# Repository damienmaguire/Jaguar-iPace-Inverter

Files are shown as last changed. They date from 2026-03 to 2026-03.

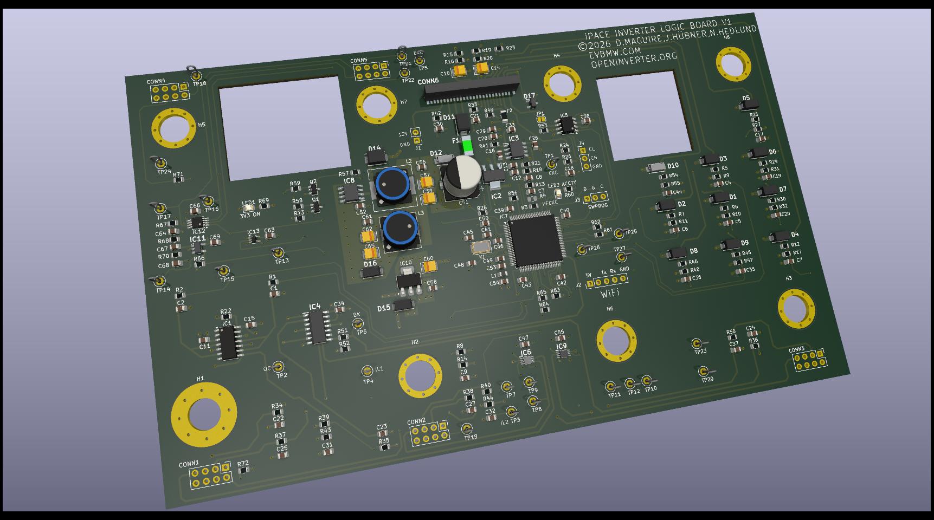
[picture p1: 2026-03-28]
Front/FDU_V1/FDU_V1_3D.jpg

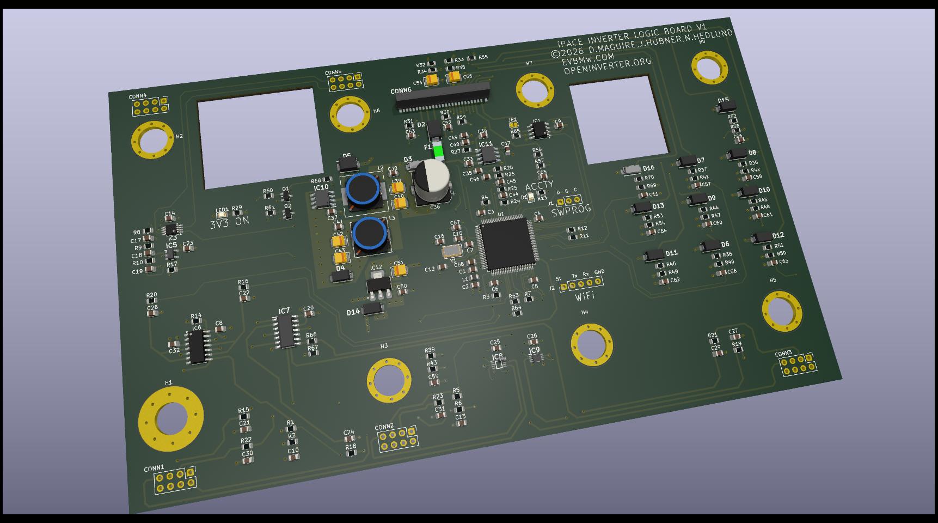
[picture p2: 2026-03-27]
Front/FDU_V1/FDU_V1_Tracked.jpg

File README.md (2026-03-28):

# Jaguar-iPace-Inverter
Design of Opensource Logic boards to run the Jaguar iPace Inverter and Motors.

PCB Designs in Kicad 9 format.

Front inverter used in the iPace is acuallly a Vitesco EPF2.8+ :
https://vitesco-technologies.com/en/Home/Solutions/Products/High-Voltage-Inverter-(EPF2-8-)-en

Reverse engineering thread on the openinverter forum :
https://openinverter.org/forum/viewtopic.php?f=23&t=1210

Videos :
https://youtu.be/Kg5qWuOF9P8

10/10/25 : Add prelim front drive unit V1 board design (work in progress).

25/03/26 : PCB Layout in progress.

FDU_V1

28/03/26 : Layout done. First prototypes ordered from JLCPCB.

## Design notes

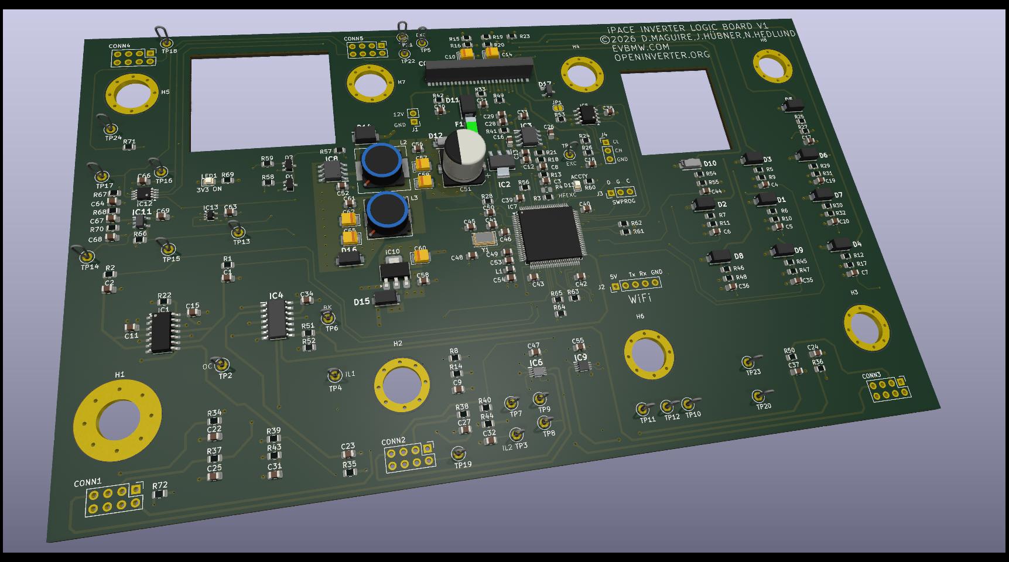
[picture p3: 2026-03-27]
Front/FDU_V1/FDU_V1_Final.jpg

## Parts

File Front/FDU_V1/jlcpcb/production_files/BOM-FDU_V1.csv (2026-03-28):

Comment | Designator | Footprint | LCSC | Quantity
0.1uF | C11,C34,C38,C39,C40,C42,C43,C46,C47,C48,C49,C50,C53,C55,C63,C66,C69 | C_0805_2012Metric | C126469 | 17
0R | R49 | R_0805_2012Metric | C17477 | 1
100R | R71,R72 | R_0805_2012Metric | C17408 | 2
100uF 6.3V | C10,C14,C57,C59,C60,C62,C65 | CP_EIA-3528-15_AVX-H | C7195 | 7
10K | R1,R17,R2,R21,R27,R33,R42,R56,R63,R66,R73 | R_0805_2012Metric | C17414 | 10
10R | R41 | R_0805_2012Metric | C17415 | 1
10nF | C15,C22,C23,C24,C25,C27,C37 | C_0805_2012Metric | C1710 | 7
10uF | C16,C33,C58 | C_0805_2012Metric | C15850 | 3
10uH 0805 | L1 | L_0805_2012Metric | C88172 | 1
1206L050/24WR | F2 | Fuse_1206_3216Metric | C2154056 | 1
120R | R53 | R_0805_2012Metric | C17437 | 1
150pF | C68 | C_0805_2012Metric | C107111 | 1
1K | R58,R59 | R_0805_2012Metric | C149504 | 2
1K | R28,R45,R46,R47,R48,R51,R61,R62,R67 | R_0805_2012Metric | C17513 | 8
1K2 | R12,R23,R24,R25,R8 | R_0805_2012Metric | C114526 | 5
1K5 | R10,R11,R31,R32,R55,R9 | R_0805_2012Metric | C114555 | 6
1K8 | R13,R18 | R_0805_2012Metric | C114222 | 2
1N5 | C64 | C_0805_2012Metric | C1717 | 1
1nF | C21,C30,C31,C32,C61 | C_0805_2012Metric | C94121 | 5
1uF | C1,C17,C18,C19,C2,C20,C26,C35,C36,C4,C5,C52,C54,C56,C6,C7,C9 | C_0805_2012Metric | C215803 | 17
1uF 25V | C44 | C_0805_2012Metric | C116352 | 1
220R | R15,R16,R19,R20 | R_0805_2012Metric | C17557 | 4
22nF | C12,C13,C28,C29,C3,C8 | C_0805_2012Metric | C1729 | 6
27K | R57 | R_0805_2012Metric | C17593 | 1
27pF | C41,C45 | C_0805_2012Metric | C1808 | 2
2K | R52 | R_0805_2012Metric | C17604 | 1
2K2 | R14,R22,R26 | R_0805_2012Metric | C114561 | 3
2K6 | R43,R44 | R_0805_2012Metric | C144568 | 2
330Pf | C67 | C_0805_2012Metric | C107116 | 1
3K9 | R3,R64 | R_0805_2012Metric | C114221 | 2
LEDS | LED1,LED2 | LED_0805_2012Metric | C84256 | 2
3uH | L3 | L_10.4x10.4_H4.8 | C31964 | 1
470uF 25V | C51 | CP_Elec_10x10 | C46550466 | 1
47K | R65 | R_0805_2012Metric | C17713 | 1
4K7 | R29,R30,R5,R54,R6,R7 | R_0805_2012Metric | C60816 | 6
560R | R34,R35,R36,R37,R38,R50 | R_0805_2012Metric | C28636 | 6
5K1 | R70 | R_0805_2012Metric | C84375 | 1
680R | R60,R69 | R_0805_2012Metric | C17798 | 2
68uH | L2 | L_12x12mm_H8mm | C9907 | 1
6K2 | R39,R40 | R_0805_2012Metric | C114535 | 2
6K8 | R68 | R_0805_2012Metric | C137409 | 1
8MHz | Y1 | Crystal_SMD_5032-2Pin_5.0x3.2mm | C115962 | 1
AMS1117-3.3 | IC10 | SOT-223-3_TabPin2 | C6186 | 1
CD74HC30M96 | IC4 | SOIC127P600X175-14N | C6540 | 1
ESDCAN01-2BLY | D17 | SOT95P255X150-3N | C53340814 | 1
FH12-50S-0.5SVA_54_ | CONN6 | FH1250S05SVA54 | C597991 | 1
JFC2410-0500TS | F1 | FUSC6126X280N | C136377 | 1
LM2901 | IC1 | SOIC-14_3.9x8.7mm_P1.27mm | C7932 | 1
MCP6291T-E_OT | IC11 | SOT95P280X145-5N | C145575 | 1
MMBT3904 | Q1,Q2 | SOT-23 | C20526 | 2
NCV8452STT3G | IC2 | SOT230P700X180-4N | C477982 | 1
SMAJ18CA | D10,D12 | DIONM5127X229N | C10768 | 2
SMAJ5.0A | D1,D15,D2,D3,D4,D5,D6,D7,D8,D9 | DIOM5127X229N | C83329 | 10
SMAJ7.0A | D16 | DIOM5026X229N | C138782 | 1
SN65HVD230 | IC5 | SOIC-8_3.9x4.9mm_P1.27mm | C12084 | 1
SN74LVC1G125DCK | IC13 | Texas_R-PDSO-G5_DCK-5 | C7833 | 1
SN74LVC3G04DCUR | IC9 | SOP50P310X90-8N | C153799 | 1
SN74LVC3G17DCTR | IC12,IC6 | MSOP-8_3x3mm_P0.65mm | C18213 | 2
SS54B | D11,D14 | DIOM5336X244N | C32513 | 2
STM32F103VCTx | IC7 | LQFP-100_14x14mm_P0.5mm | C53327627 | 1
TDA2822D | IC3 | SOIC127P600X175-8N | C668663 | 1
XL1509-5.0E1 | IC8 | SOIC127P600X175-8N | C61063 | 1

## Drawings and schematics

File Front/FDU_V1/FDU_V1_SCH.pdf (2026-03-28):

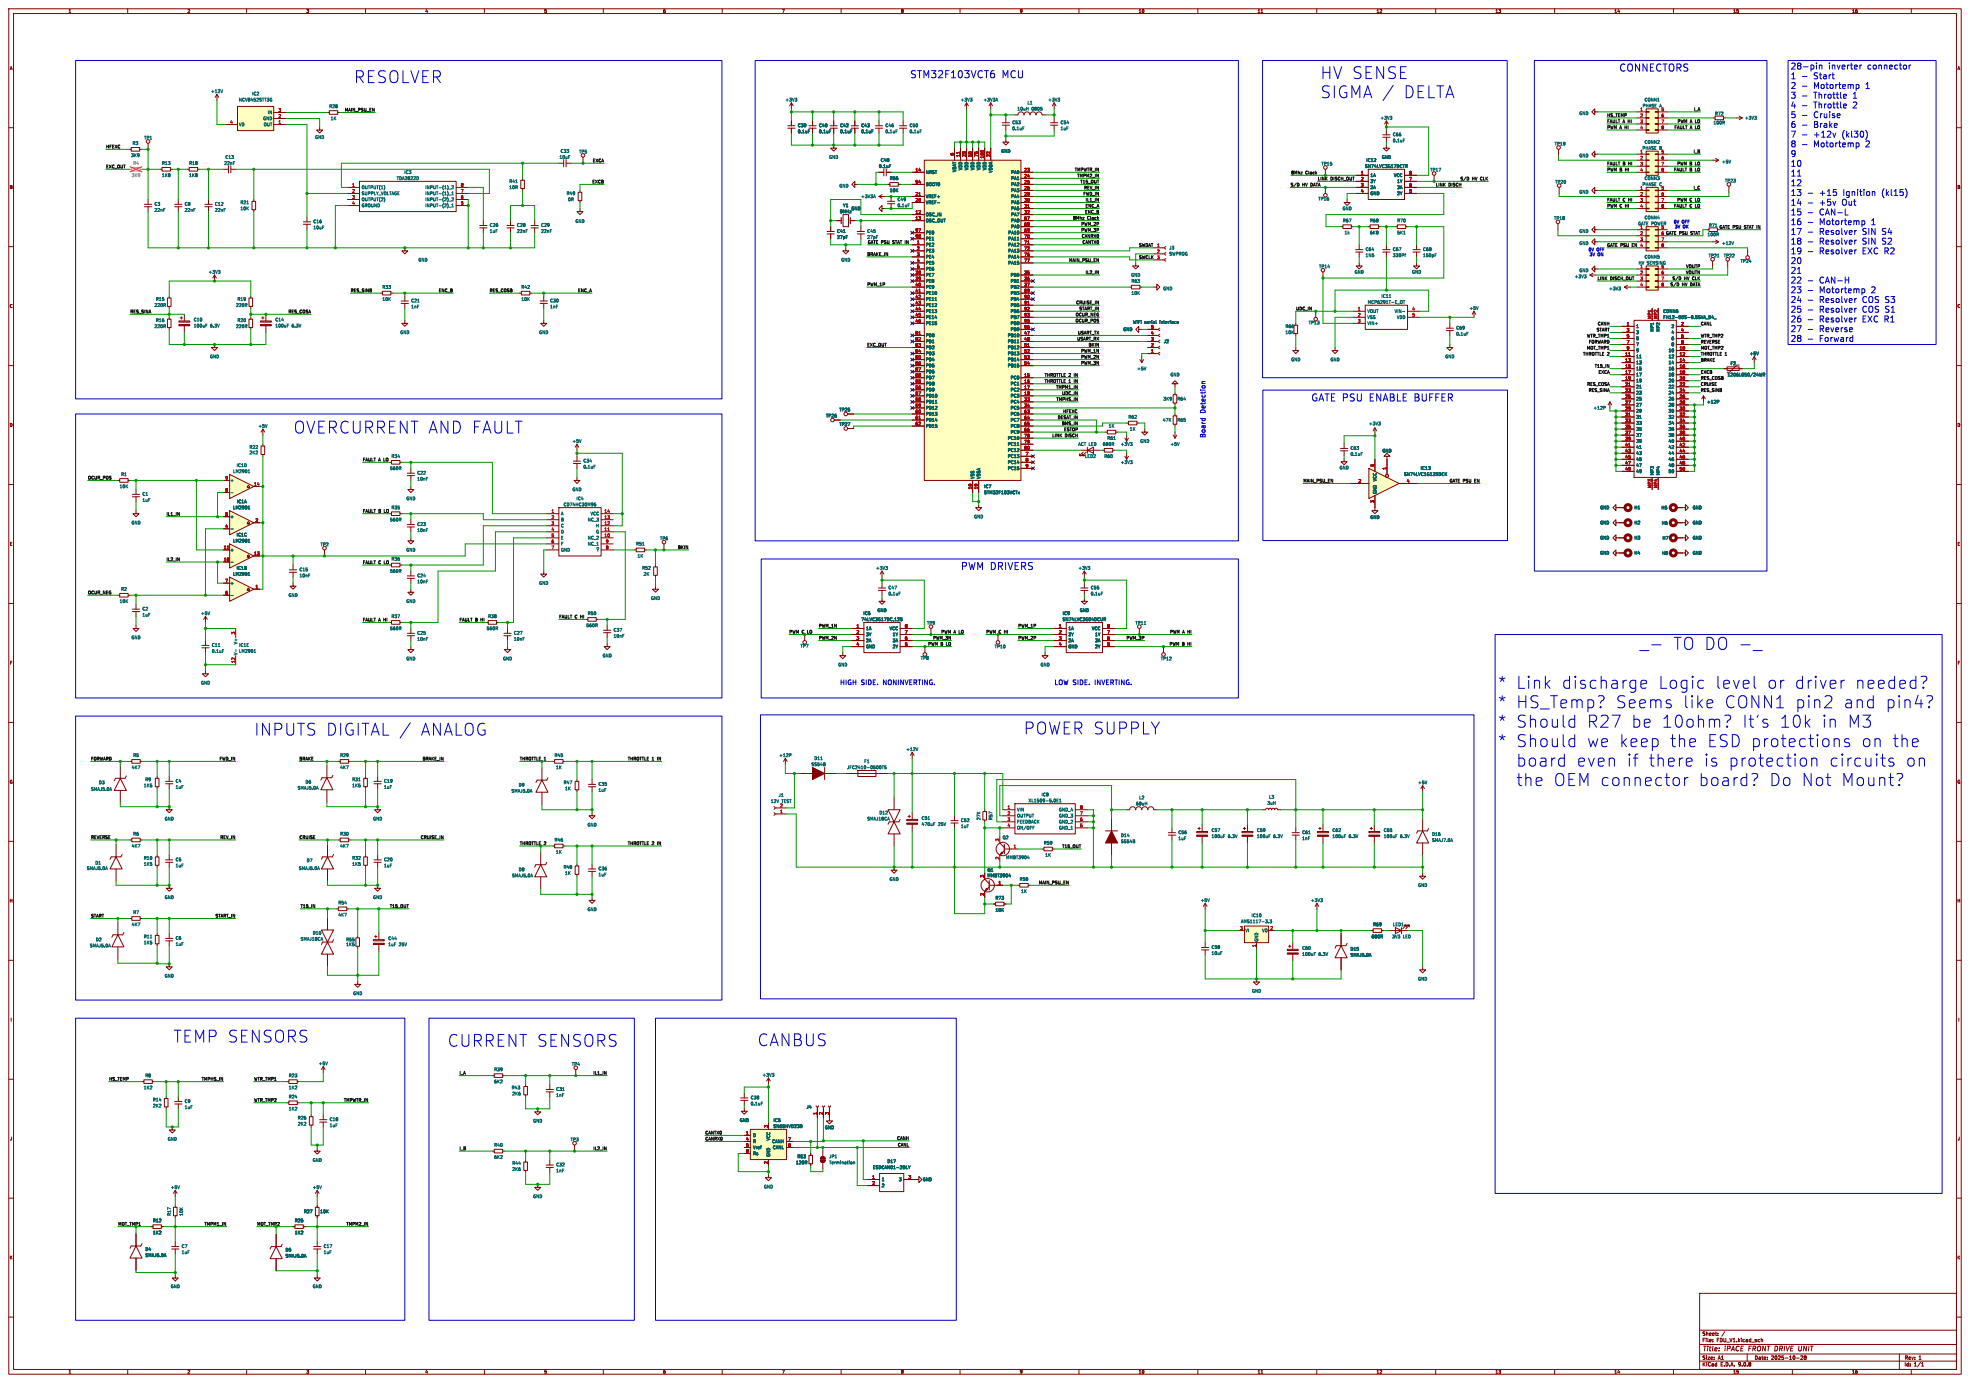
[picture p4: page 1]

6 VDD 11 VDD 28 VDD 50 VSS 10 VDD 75 VSSA 19 VDD 100 VDDA 22 PA0

FAULT B HI FAULT C HI

PWM B HI MOT_TMP1 PWM C LO

GATE PSU ENABLE BUFFER

PWM A HI FAULT A LO

* Link discharge Logic level or driver needed?
* HS_Temp? Seems like CONN1 pin2 and pin4?
* Should R27 be 10ohm? It's 10k in M3
the OEM connector board? Do Not Mount?

File: FDU_V1.kicad_sch Sheet: /
Id: 1/1 Title: iPACE FRONT DRIVE UNIT

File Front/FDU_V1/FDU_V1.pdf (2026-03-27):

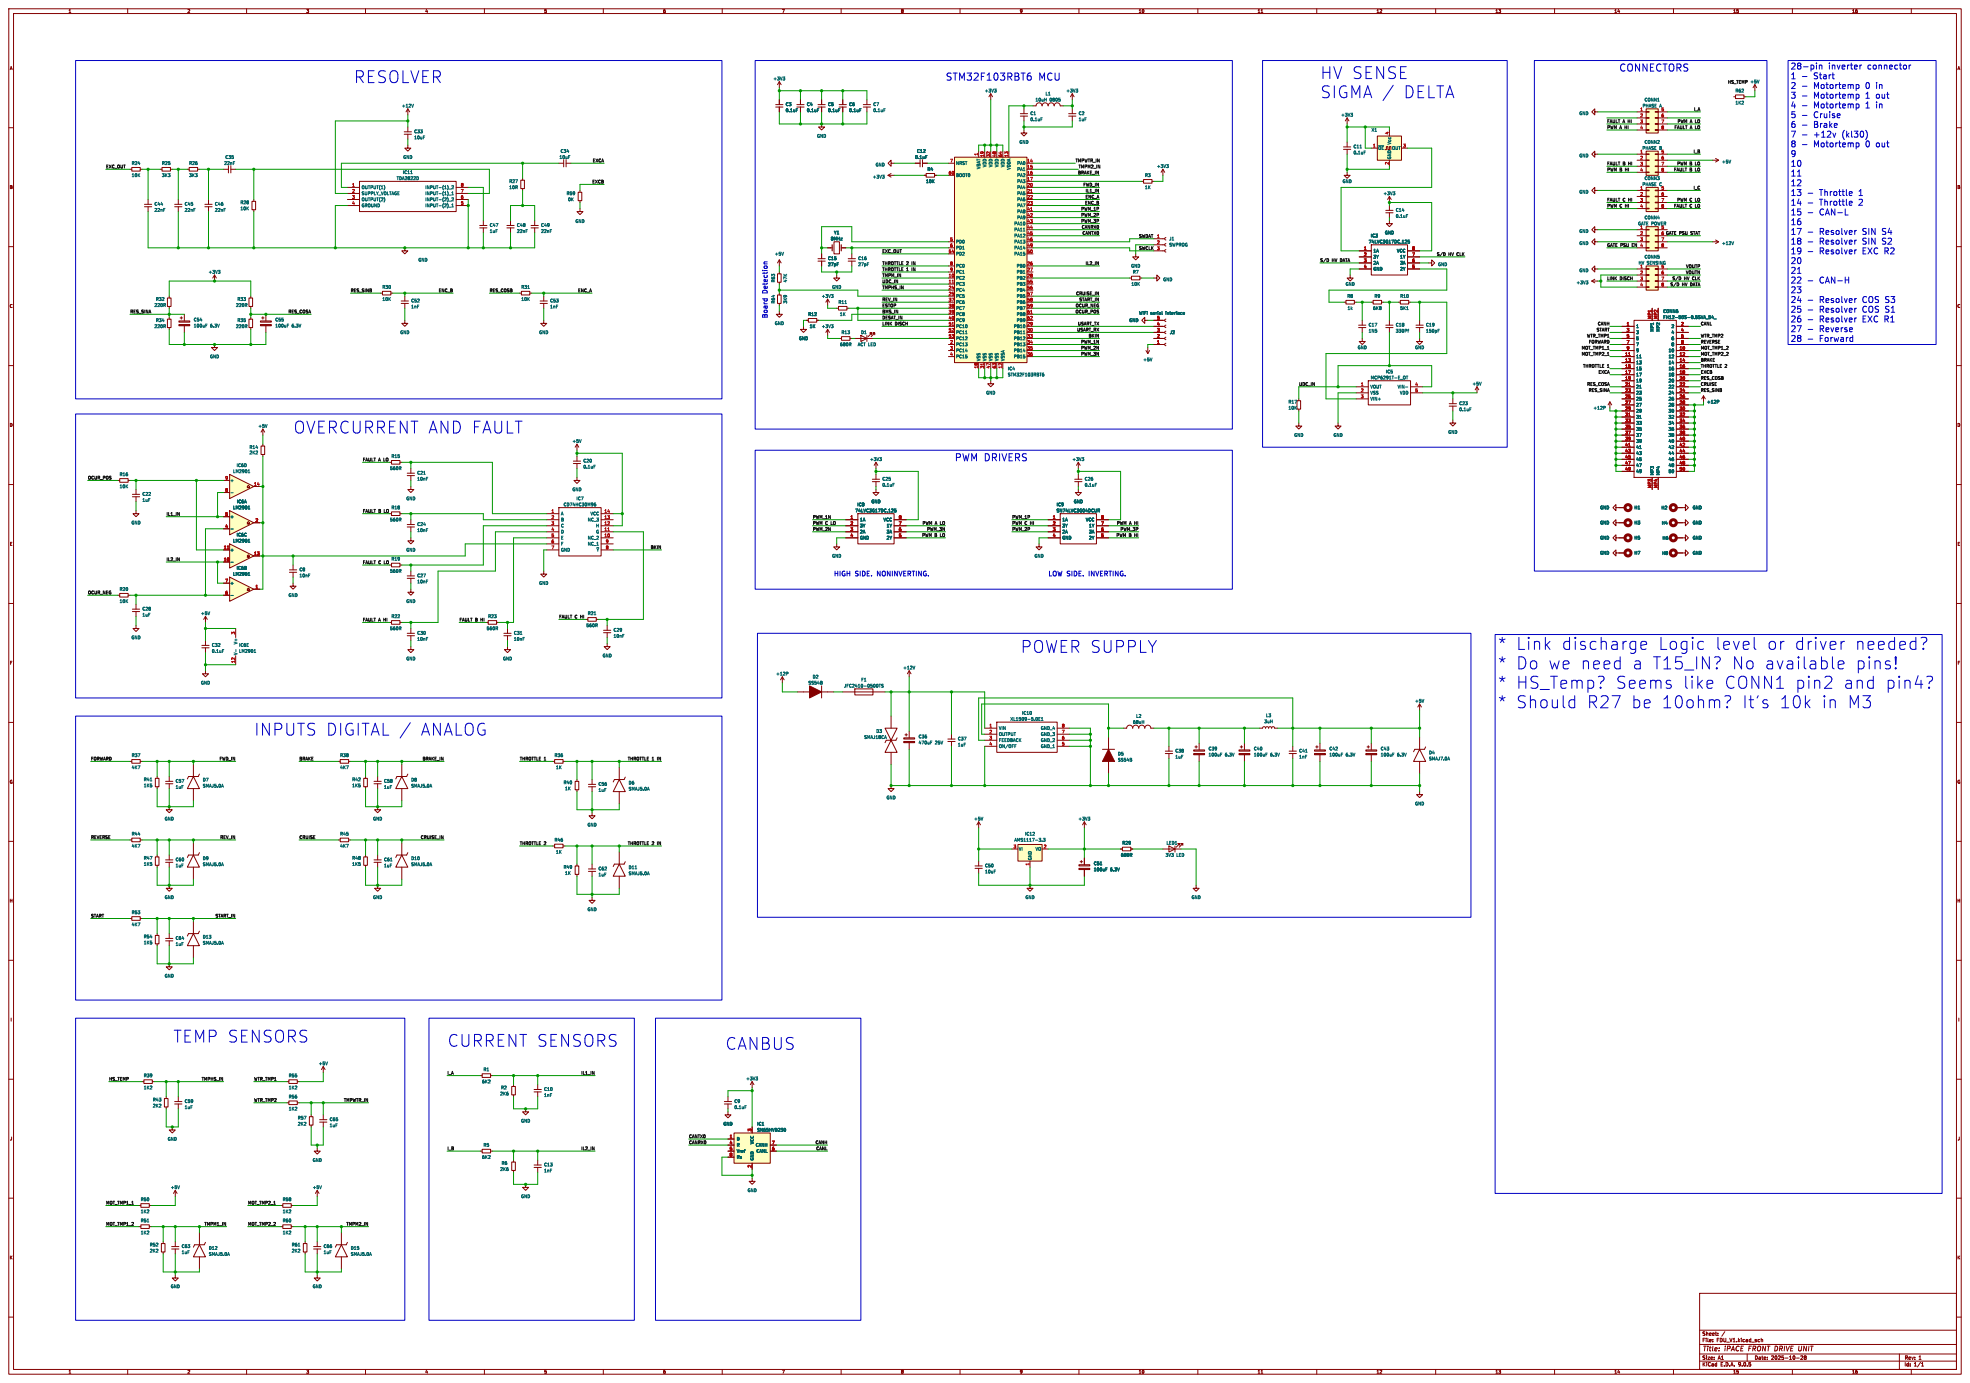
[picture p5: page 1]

HS_TEMP * Link discharge Logic level or driver needed?

1 VSS 18 VDD 19 VSS 31 VDD 32 VSS 47 VDD 48 VSS 63 VDD 64 VSSA 12 VDDA 13 PA0

FAULT C HI PWM C HI GATE PSU EN

* Do we need a T15_IN? No available pins!
* HS_Temp? Seems like CONN1 pin2 and pin4?
* Should R27 be 10ohm? It's 10k in M3

File: FDU_V1.kicad_sch Sheet: /
Id: 1/1 Title: iPACE FRONT DRIVE UNIT

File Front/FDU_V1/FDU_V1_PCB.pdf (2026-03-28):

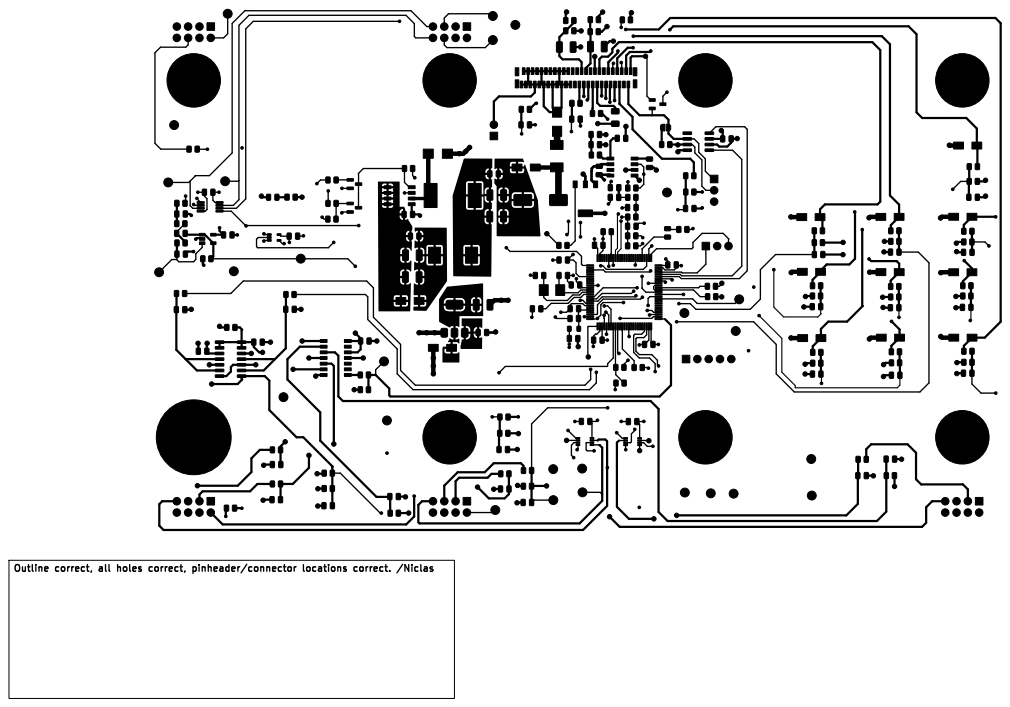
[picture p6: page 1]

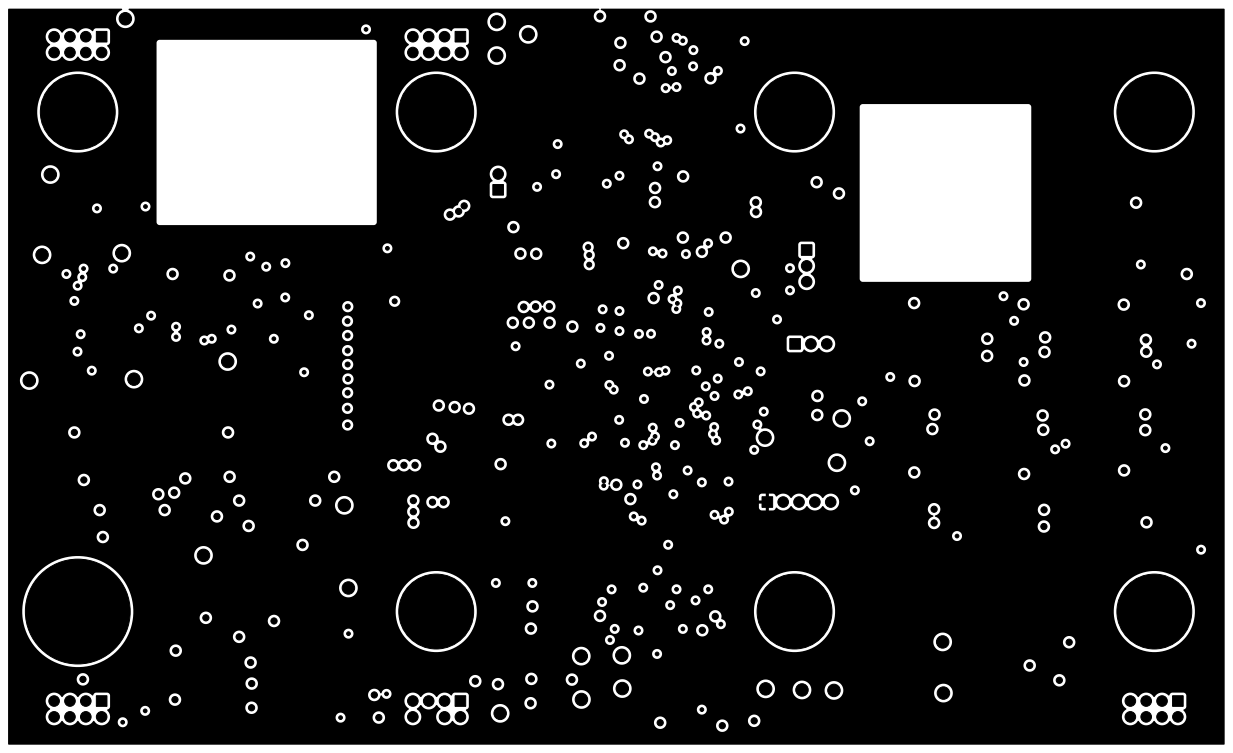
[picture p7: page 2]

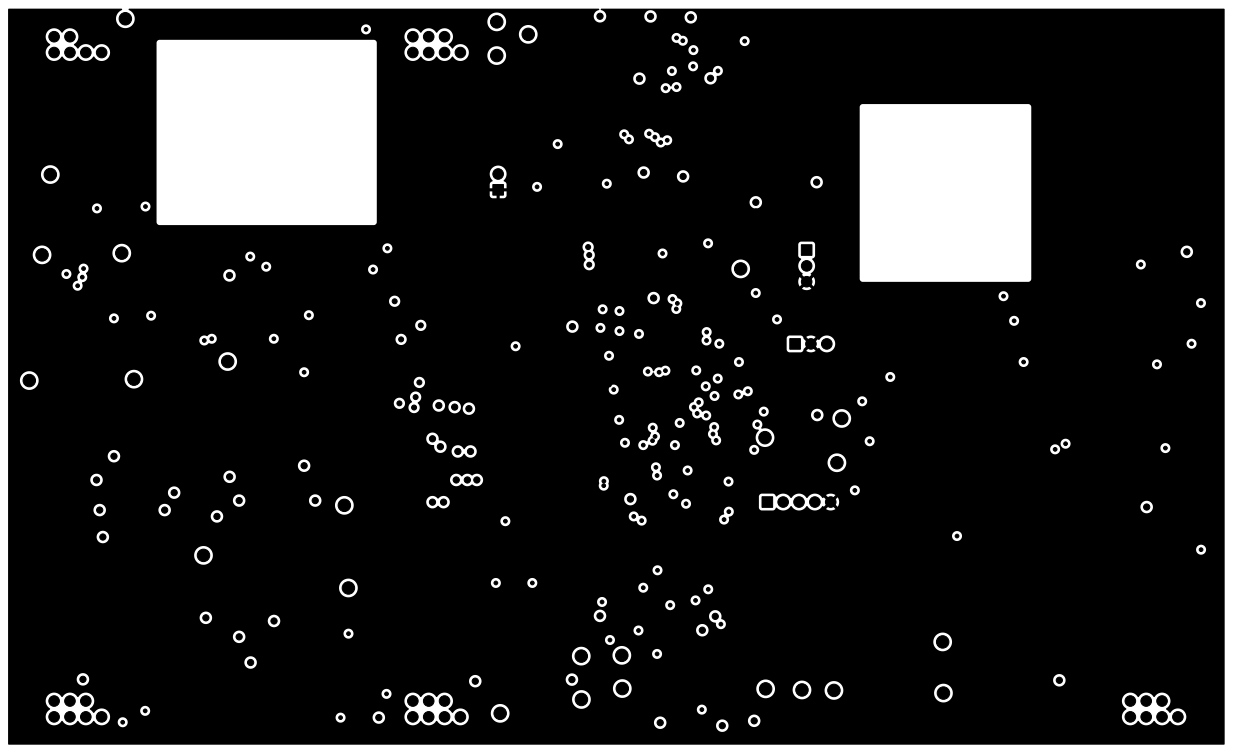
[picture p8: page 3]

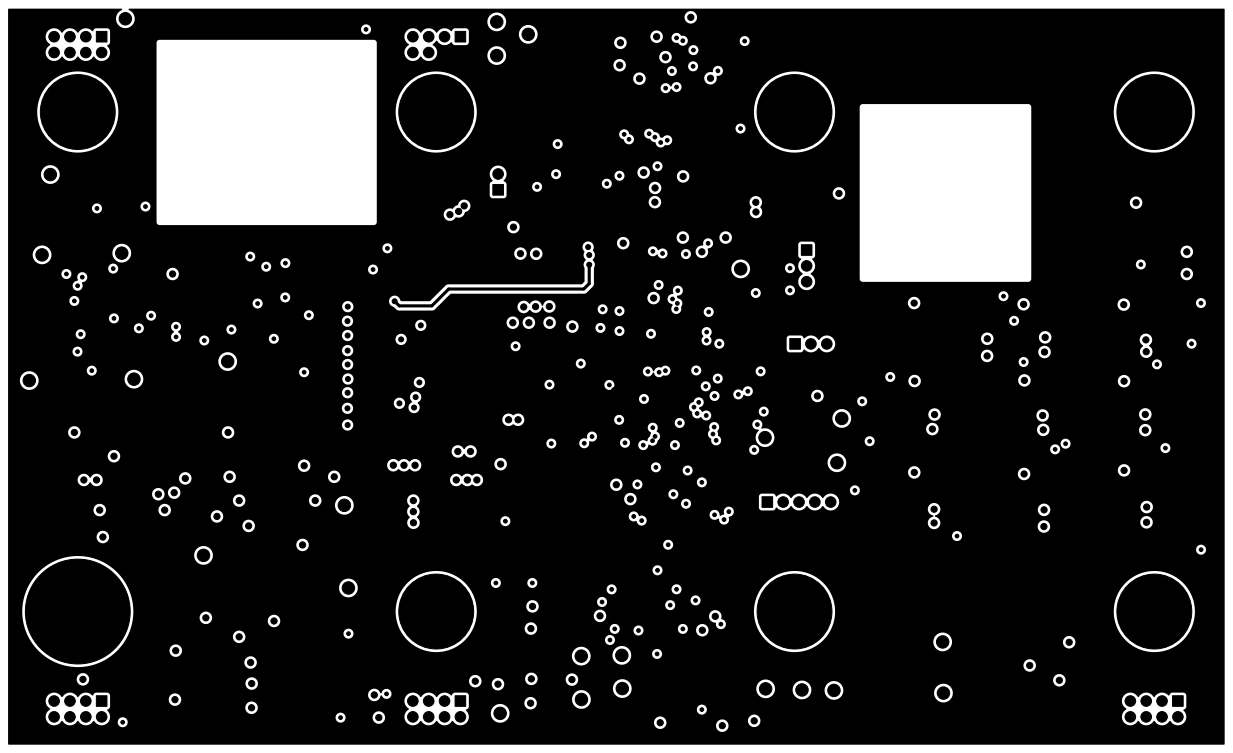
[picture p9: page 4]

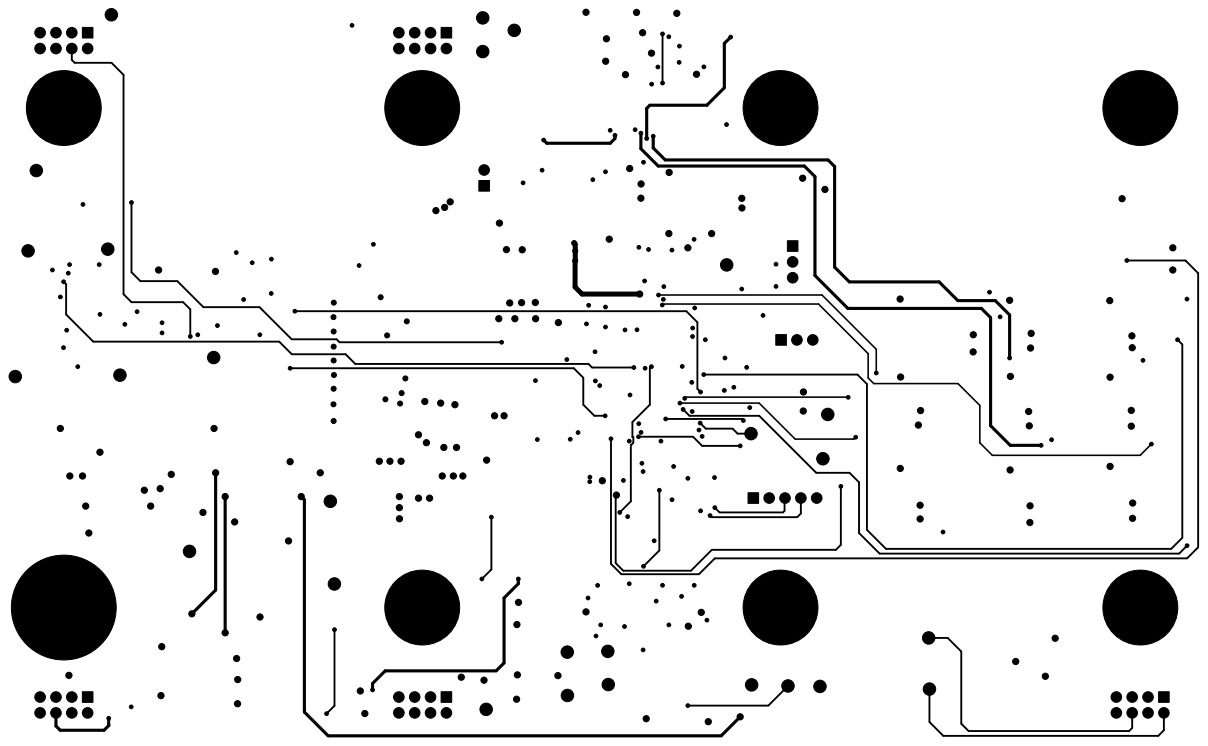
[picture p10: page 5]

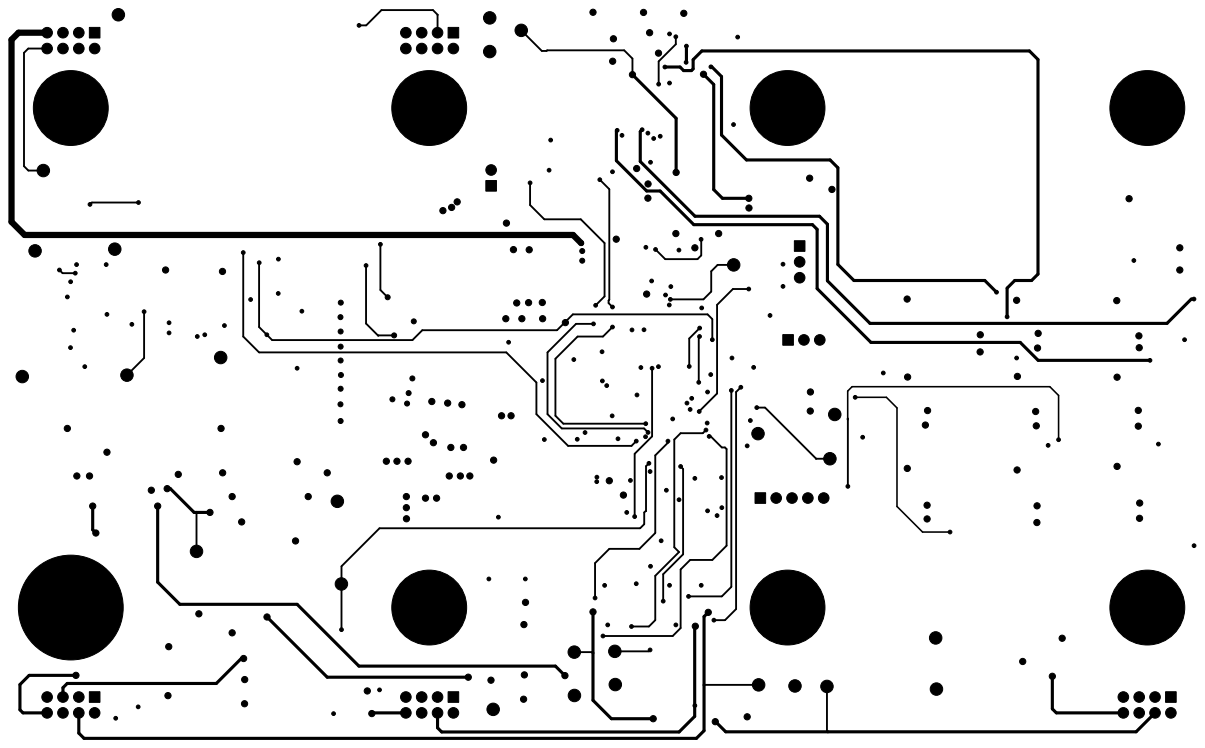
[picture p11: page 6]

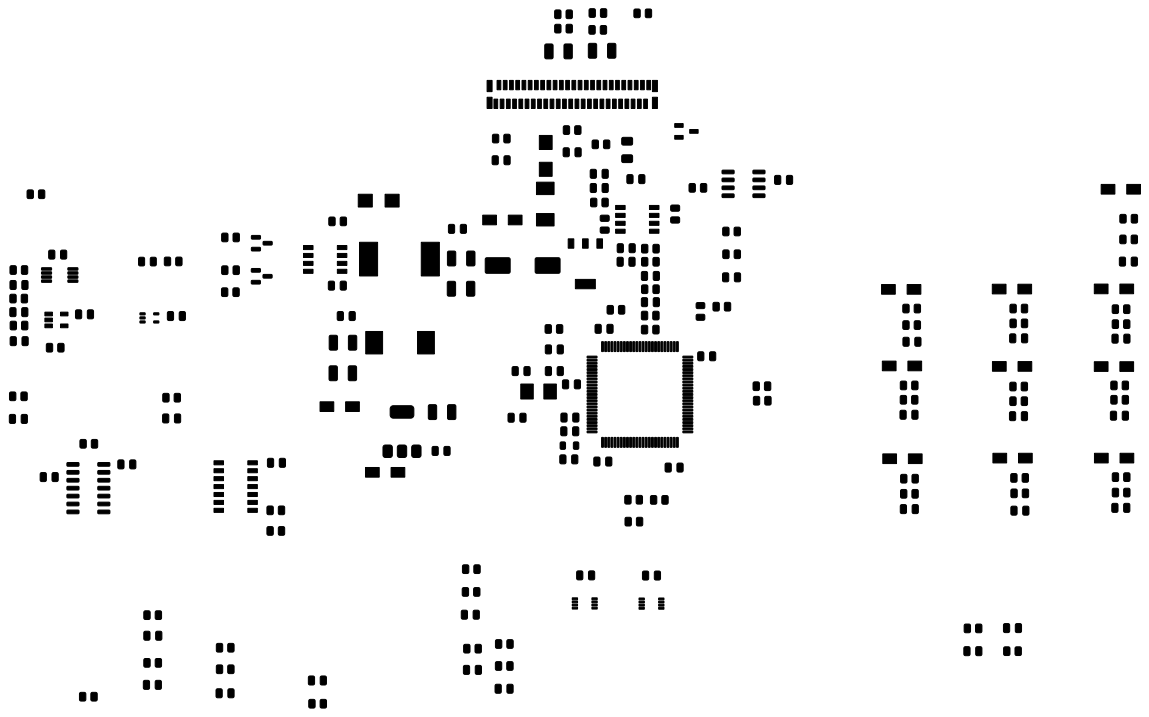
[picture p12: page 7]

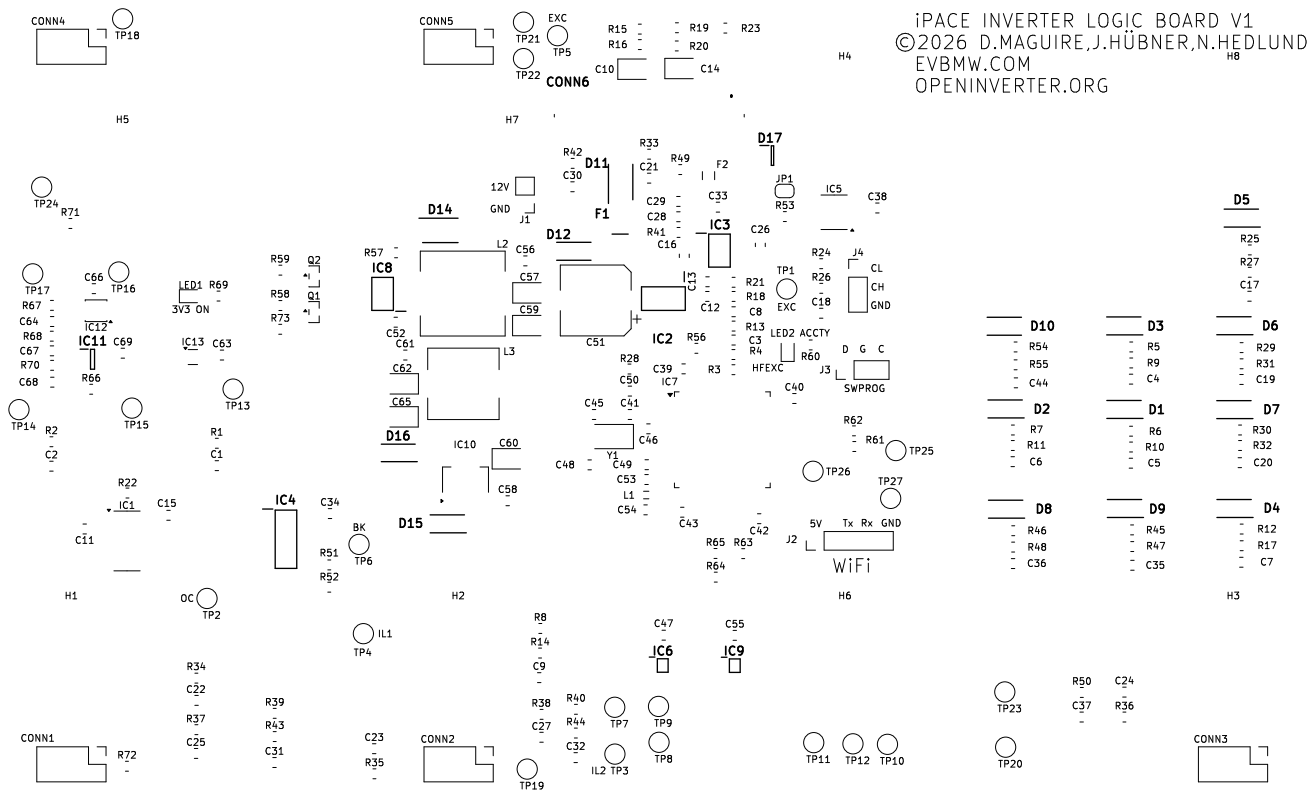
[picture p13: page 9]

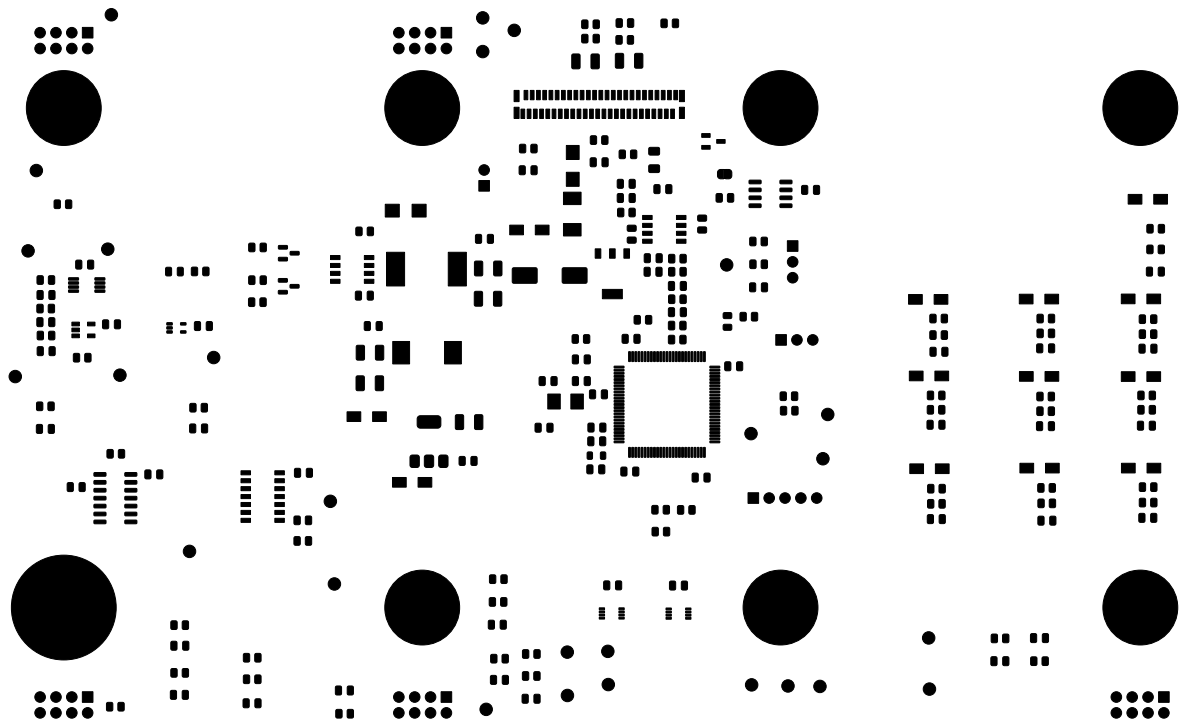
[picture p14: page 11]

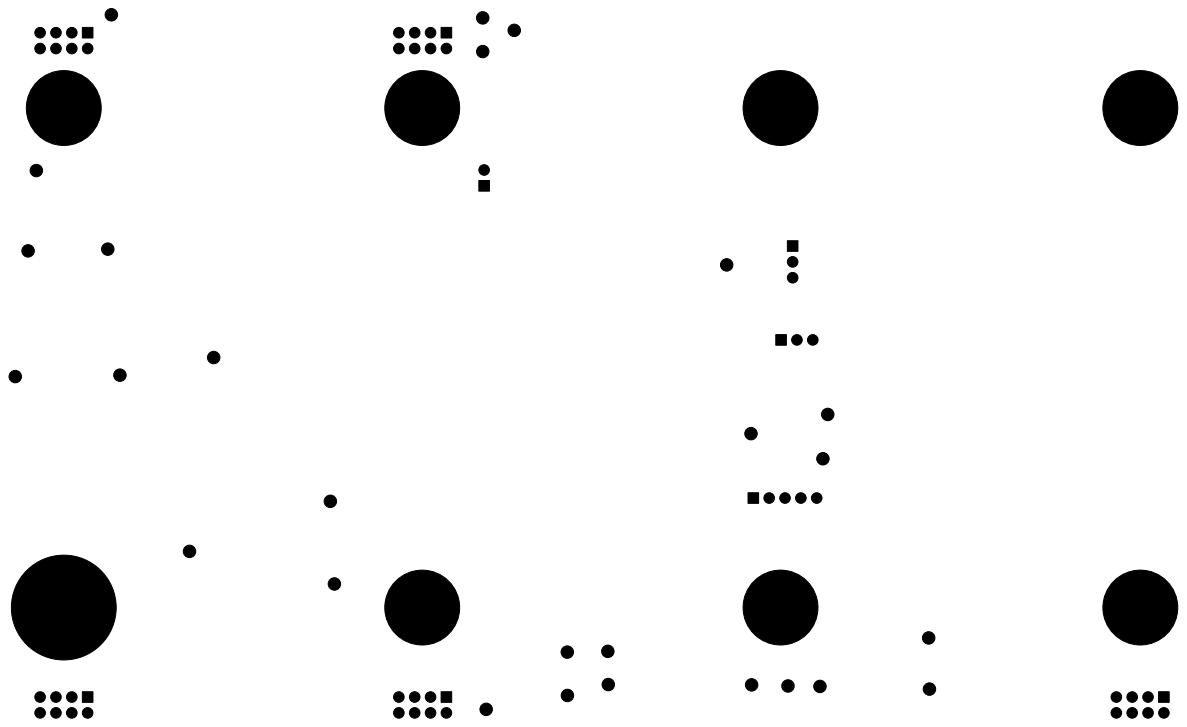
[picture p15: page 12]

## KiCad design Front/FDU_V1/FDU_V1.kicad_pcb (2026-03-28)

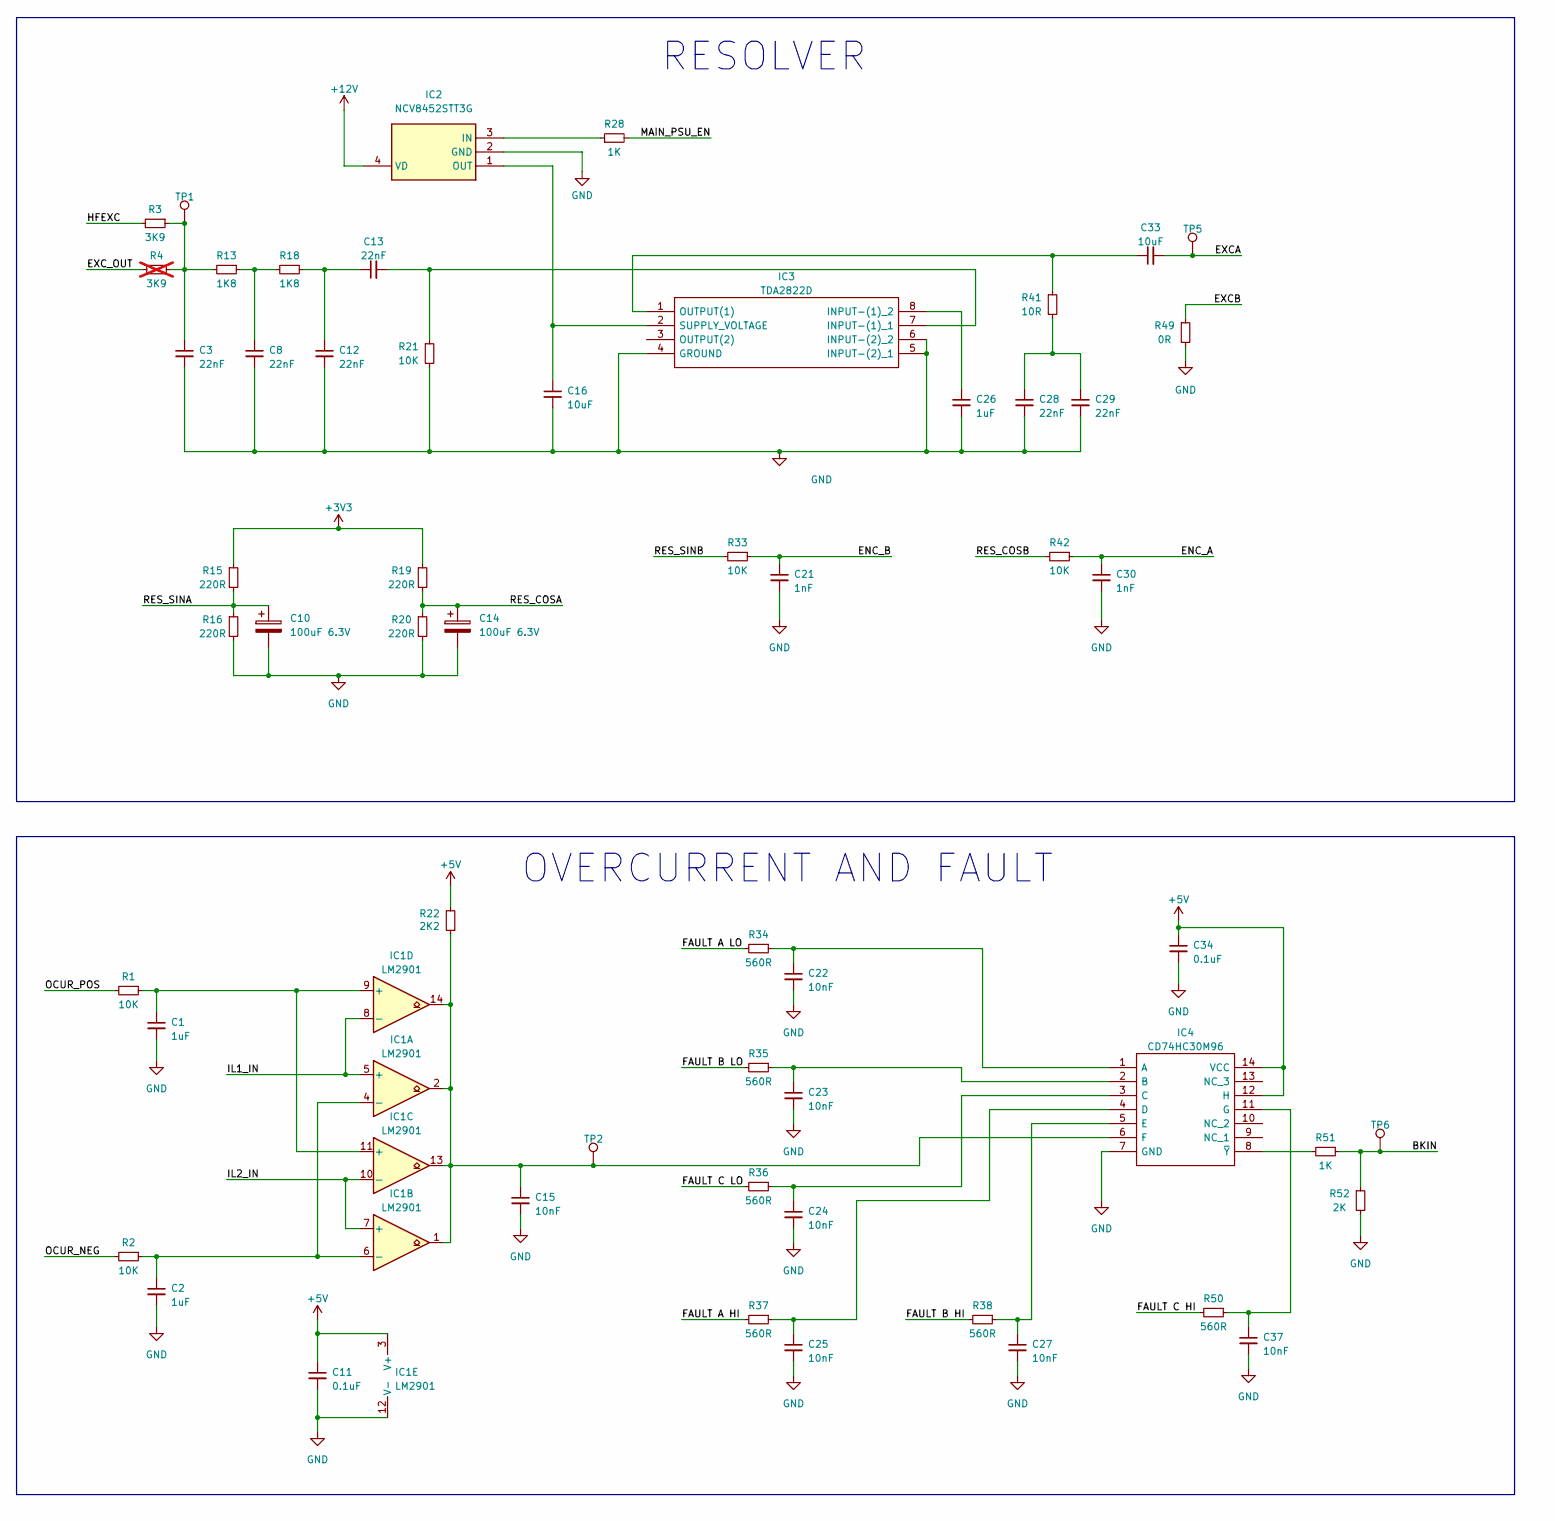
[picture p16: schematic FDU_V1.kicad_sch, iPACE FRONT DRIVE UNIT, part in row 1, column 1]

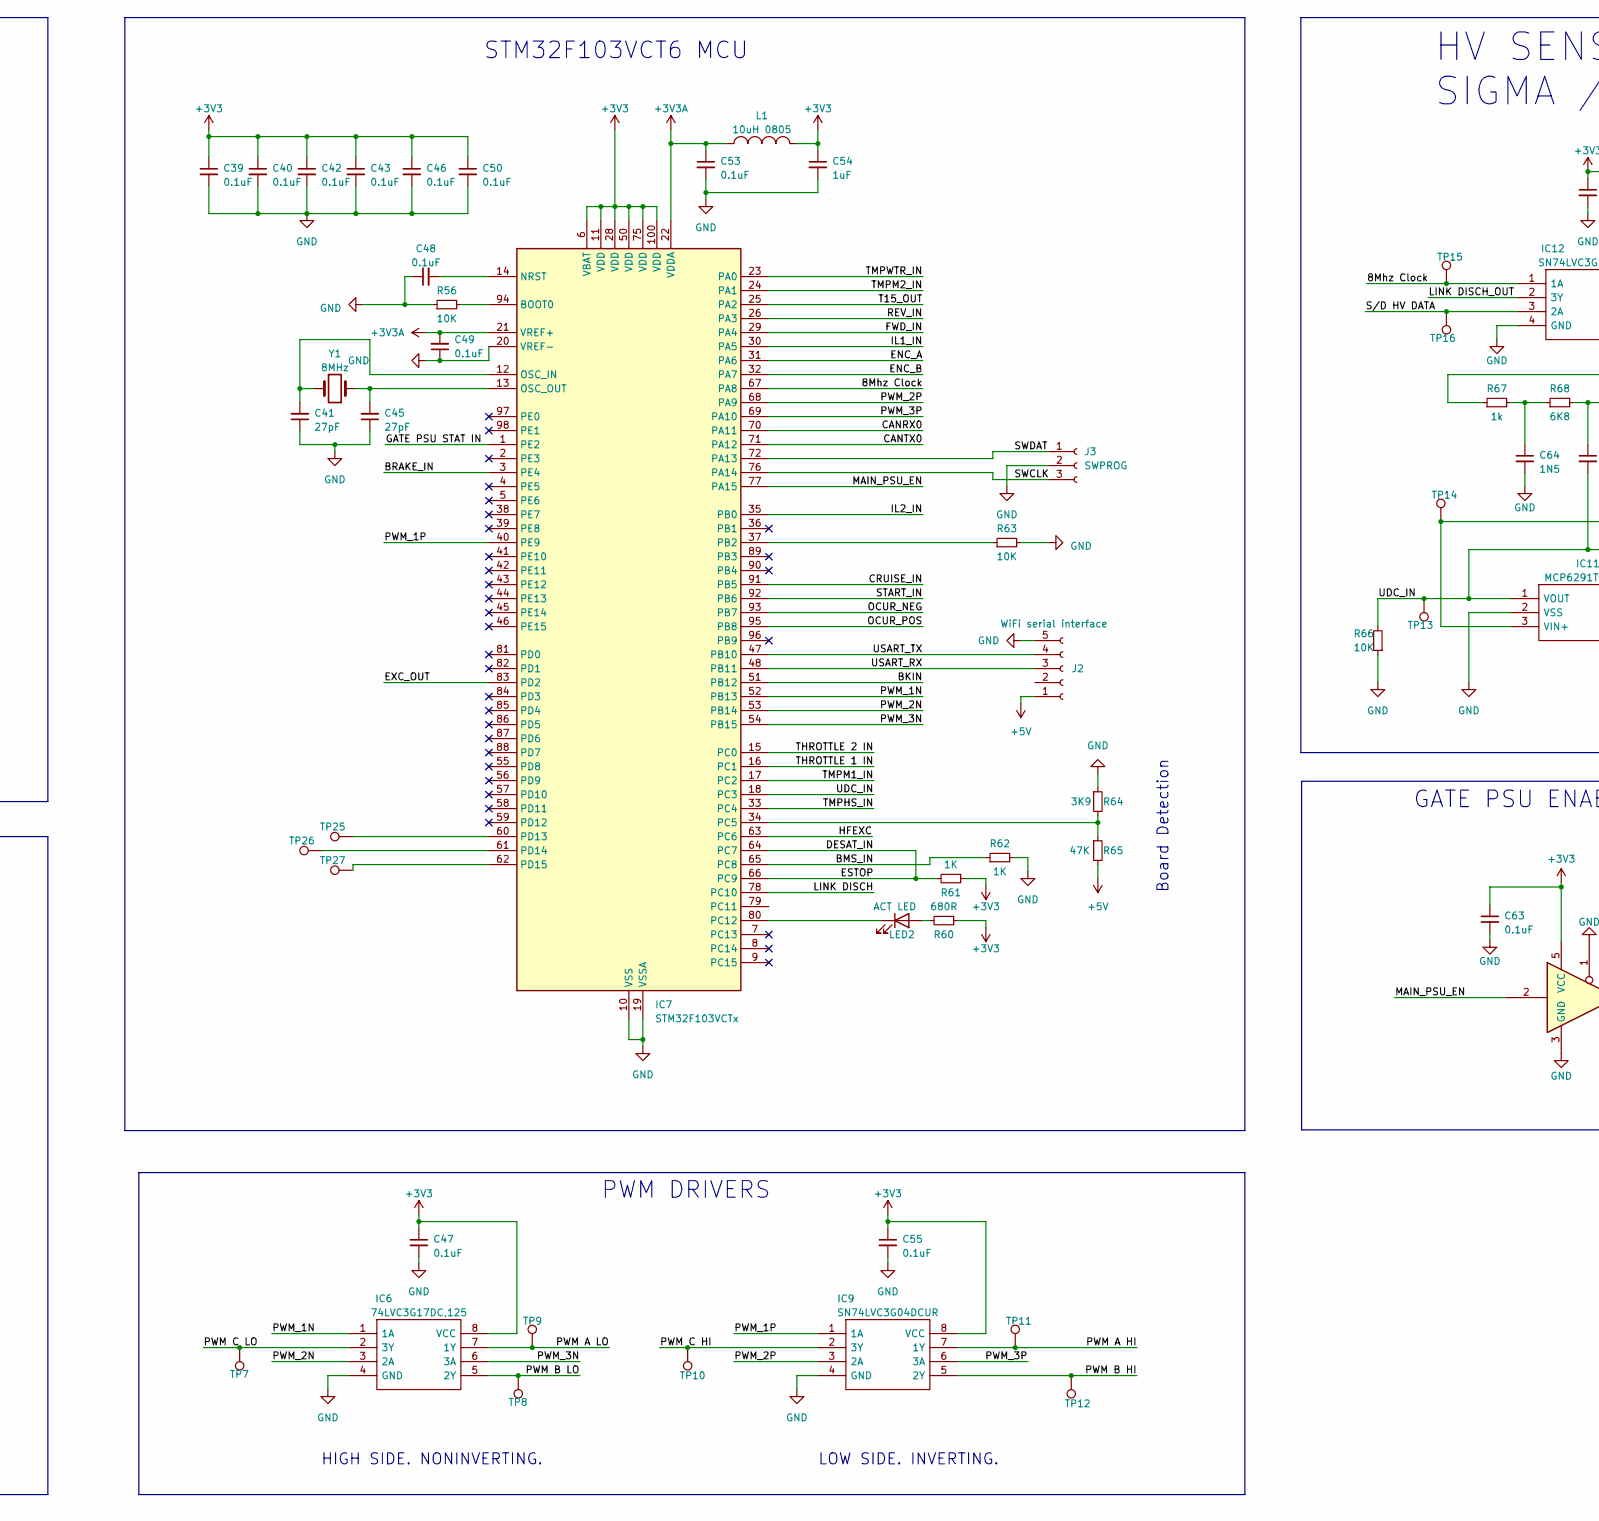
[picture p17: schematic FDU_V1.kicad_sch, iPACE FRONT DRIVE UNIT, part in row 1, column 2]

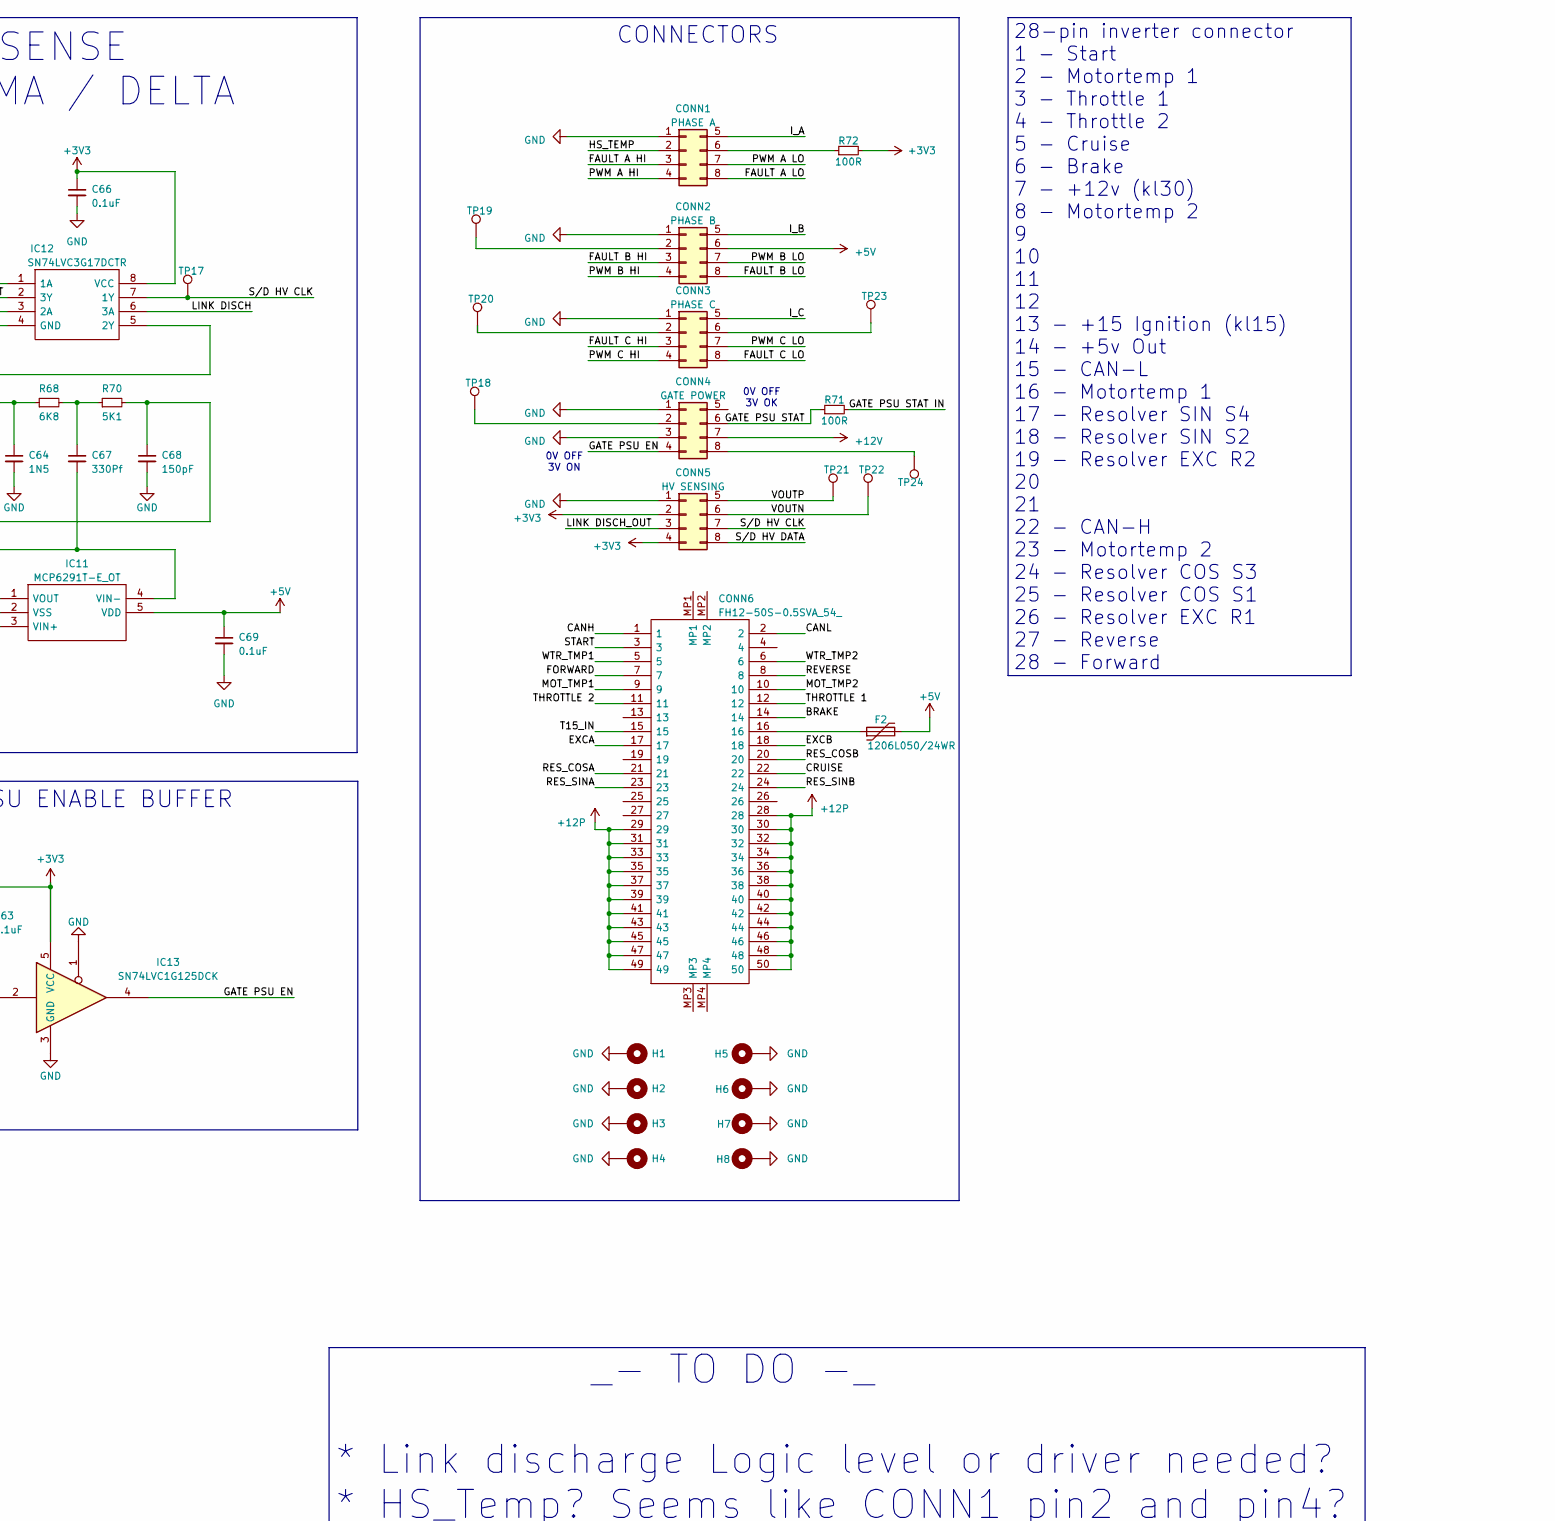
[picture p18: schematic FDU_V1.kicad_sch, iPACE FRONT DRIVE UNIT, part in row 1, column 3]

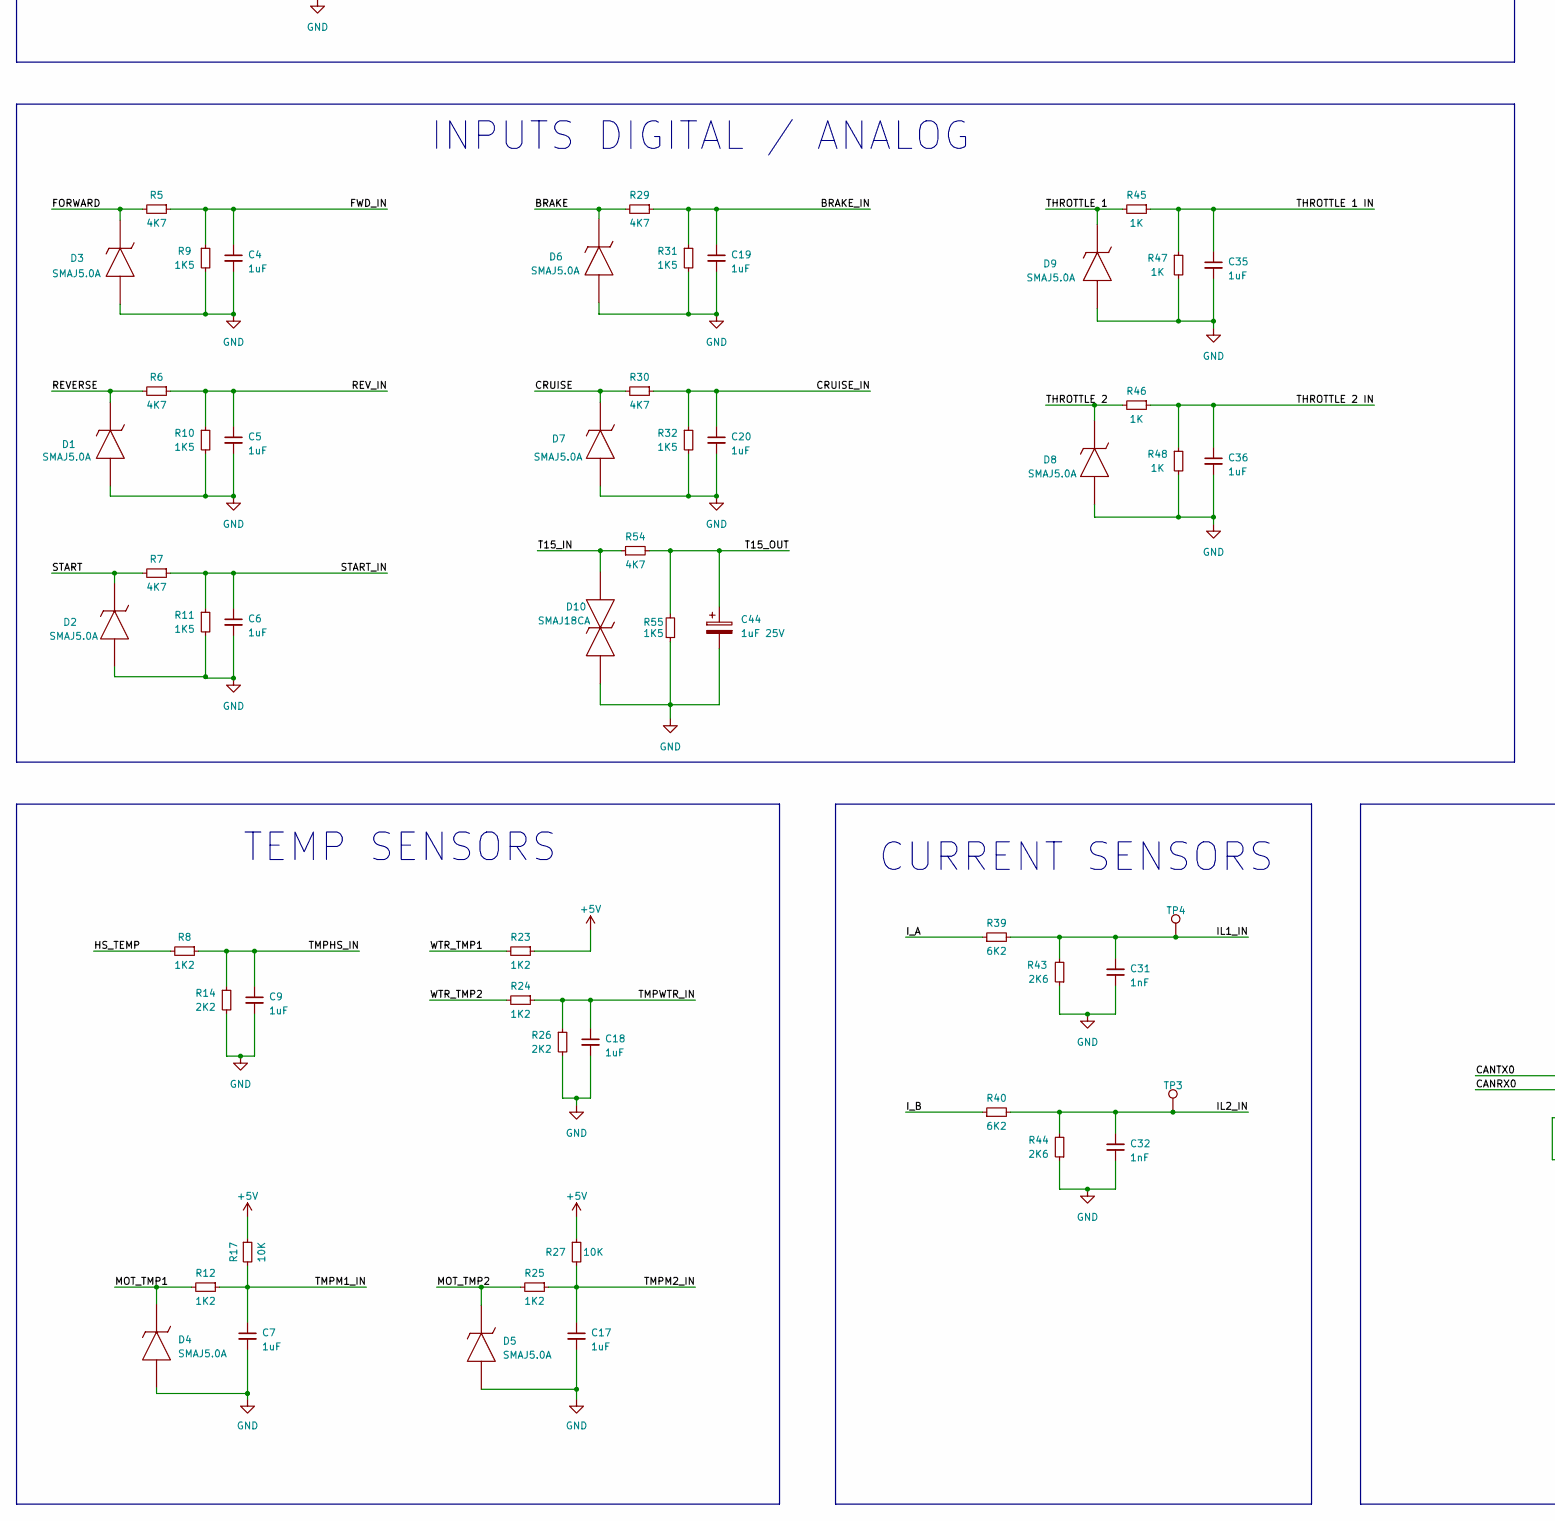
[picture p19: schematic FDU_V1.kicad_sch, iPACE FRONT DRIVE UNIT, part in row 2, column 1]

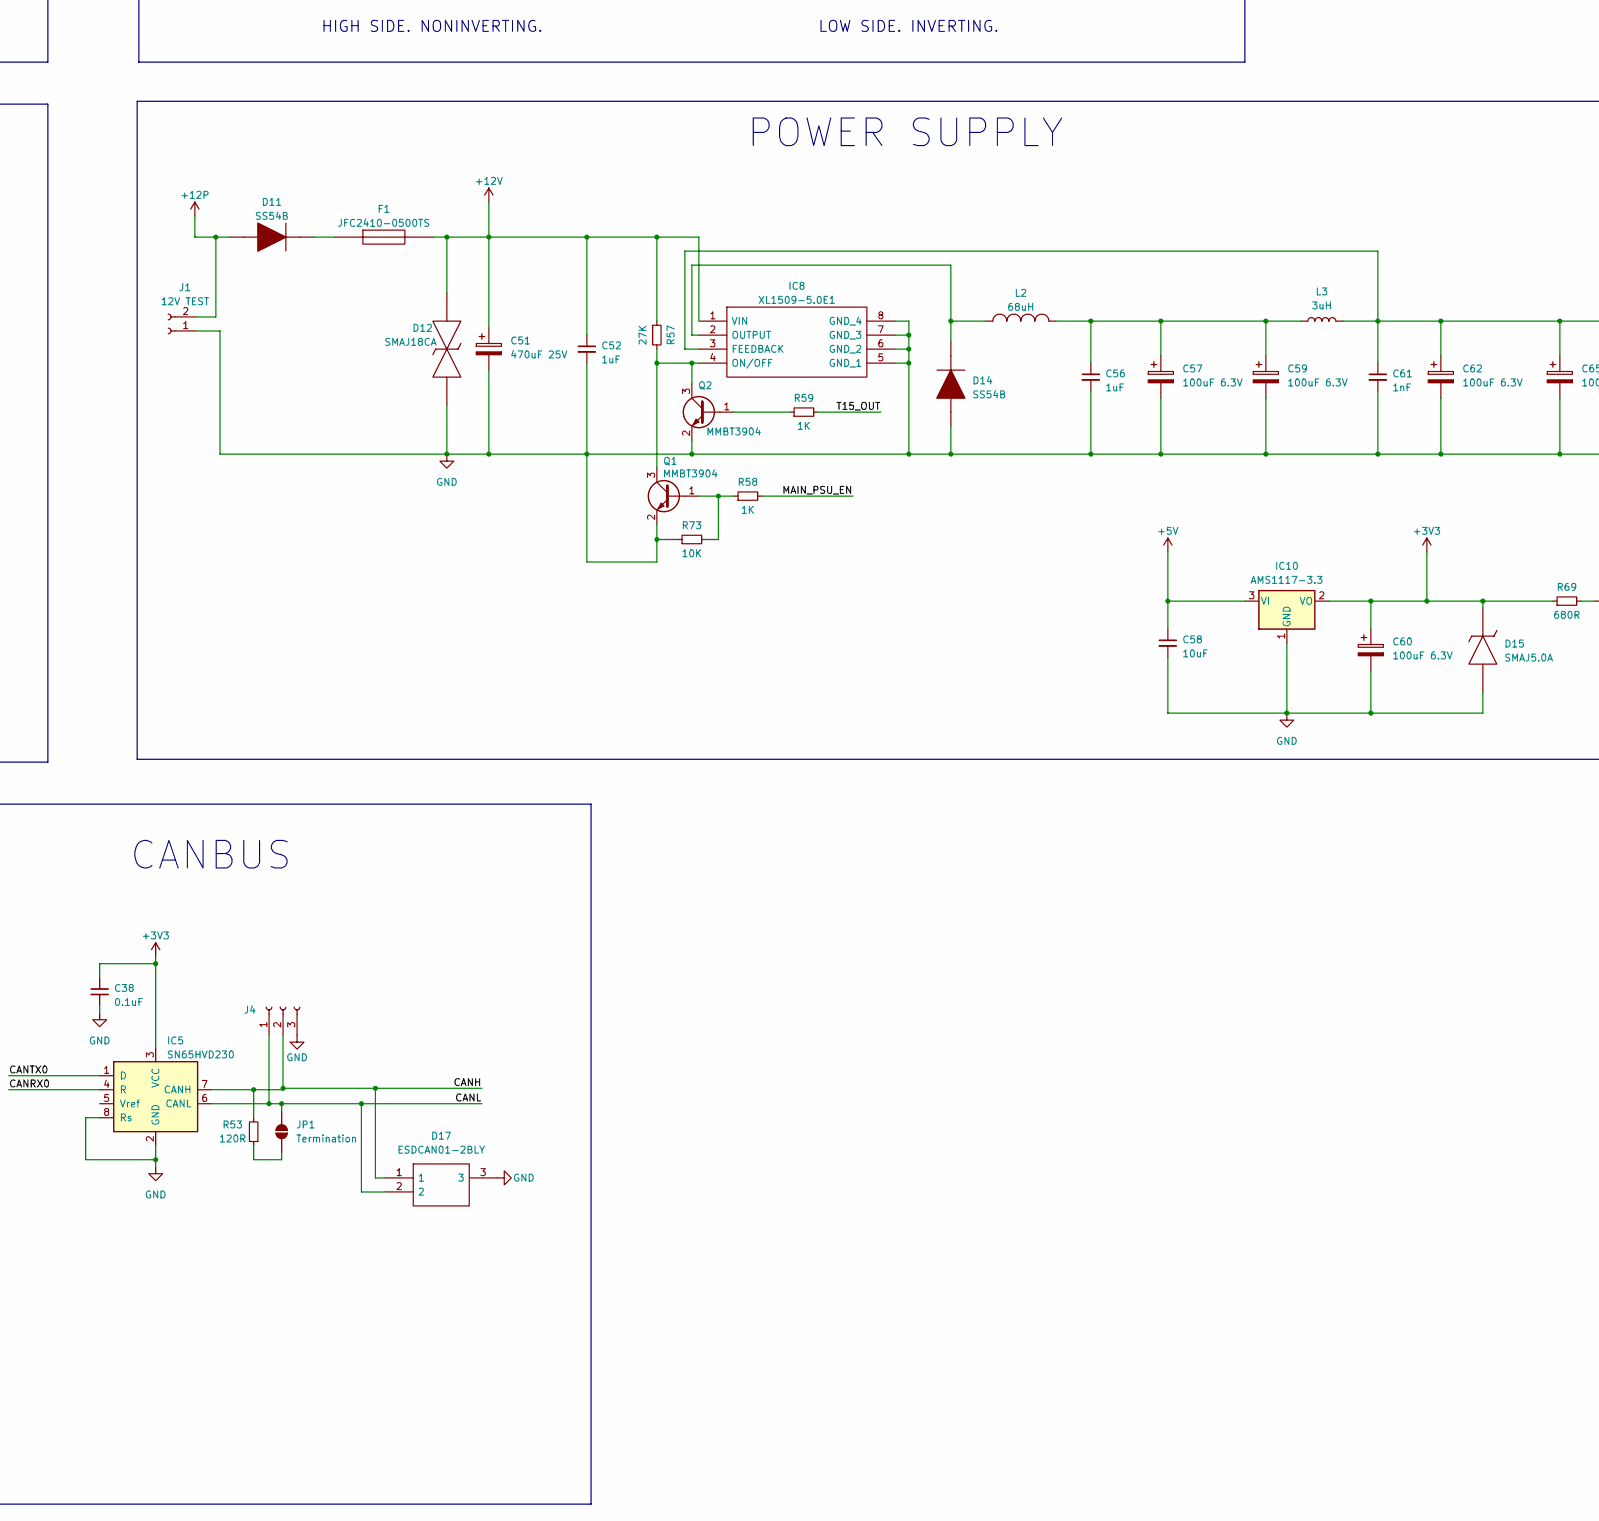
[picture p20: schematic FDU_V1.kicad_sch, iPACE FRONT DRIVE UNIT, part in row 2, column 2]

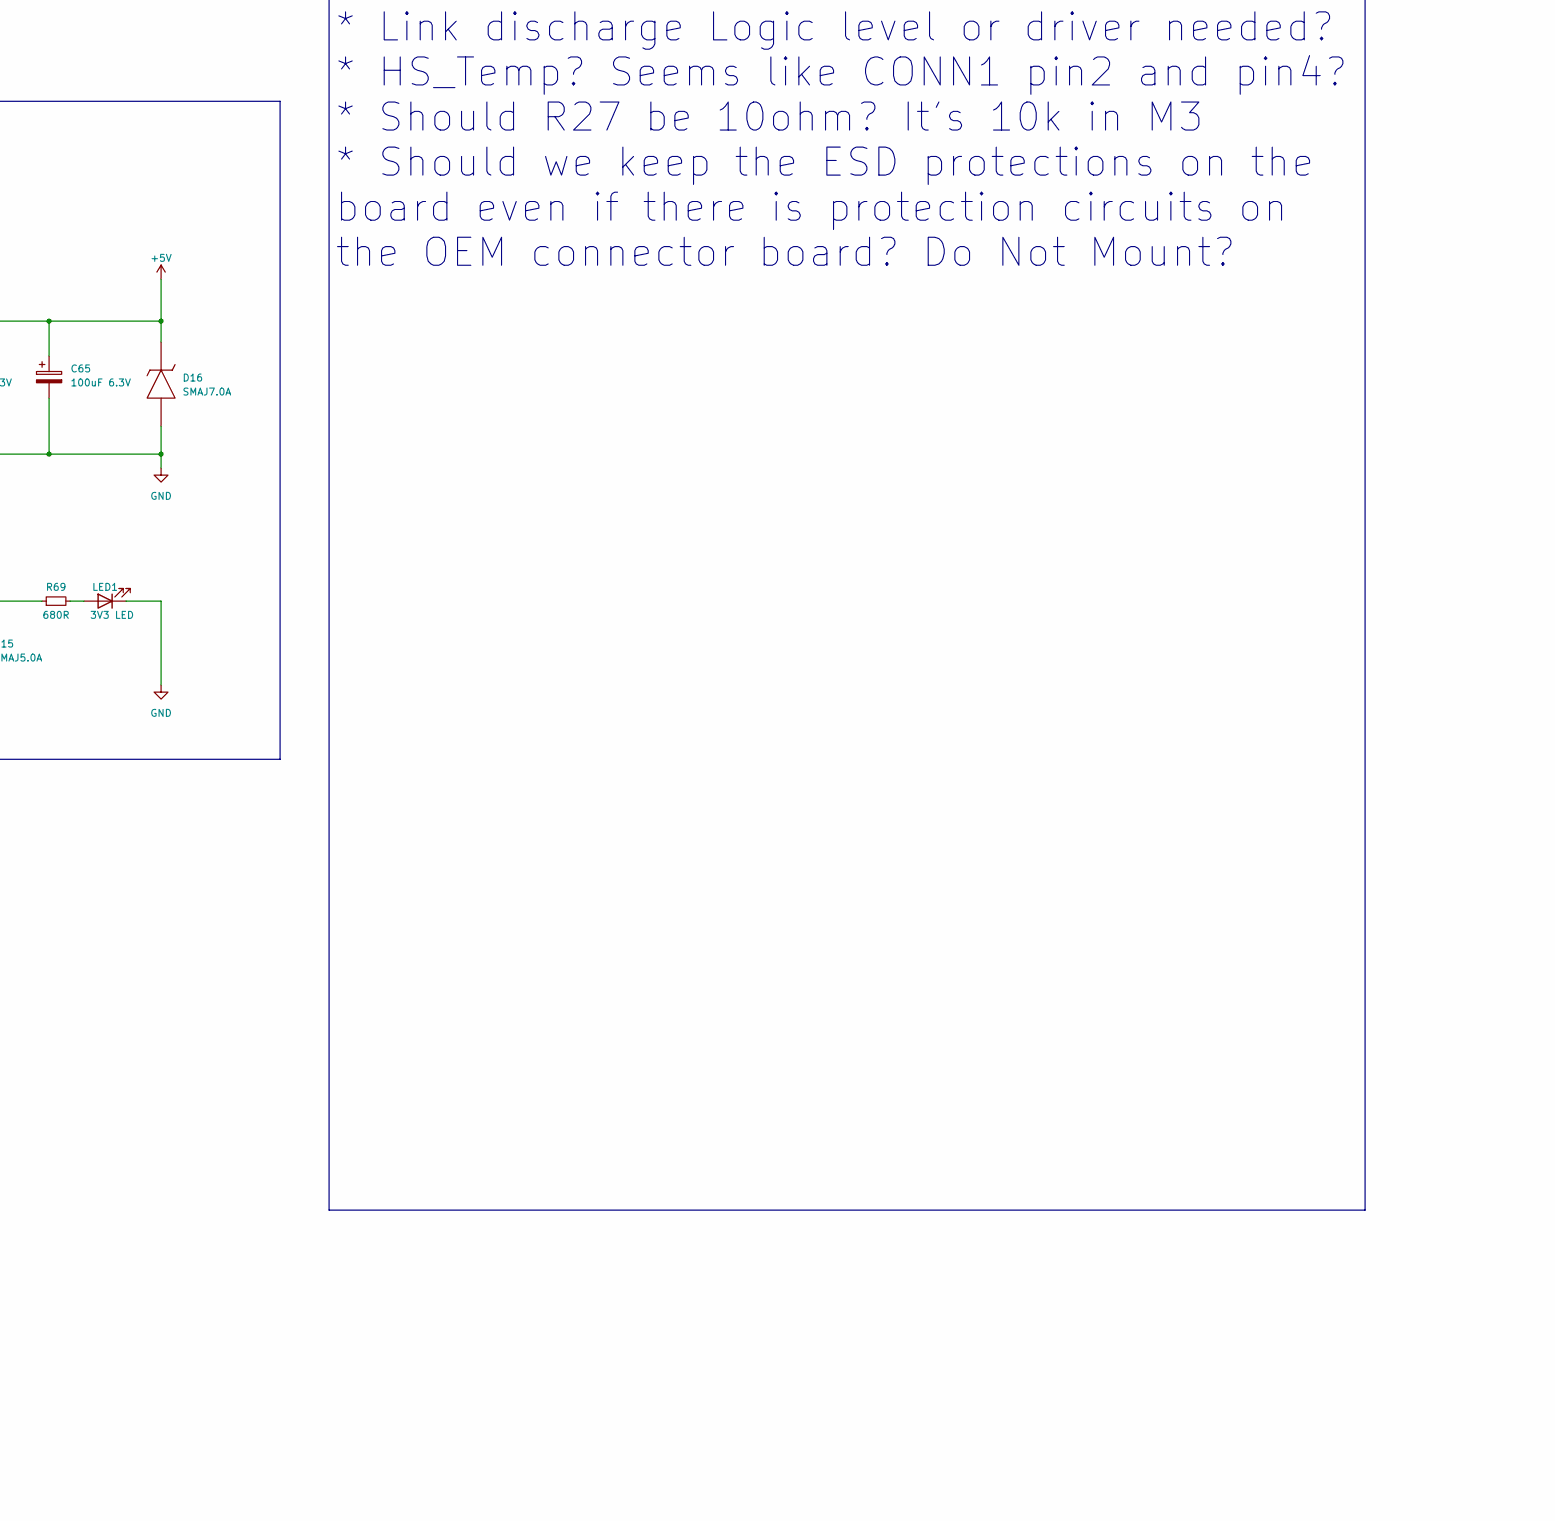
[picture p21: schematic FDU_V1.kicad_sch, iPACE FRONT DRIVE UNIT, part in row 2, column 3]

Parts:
C1, C2, C4, C5, C6, C7, C9, C17, C18, C19, C20, C26, C35, C36, C52, C54, C56: 1uF; C_0805_2012Metric
C3, C8, C12, C13, C28, C29: 22nF; C_0805_2012Metric
C10, C14, C57, C59, C60, C62, C65: 100uF 6.3V; CP_EIA-3528-15_AVX-H
C11, C34, C38, C39, C40, C42, C43, C46, C47, C48, C49, C50, C53, C55, C63, C66, C69: 0.1uF; C_0805_2012Metric
C15, C22, C23, C24, C25, C27, C37: 10nF; C_0805_2012Metric
C16, C33, C58: 10uF; C_0805_2012Metric
C21, C30, C31, C32, C61: 1nF; C_0805_2012Metric
C41, C45: 27pF; C_0805_2012Metric
C44: 1uF 25V; C_0805_2012Metric
C51: 470uF 25V; CP_Elec_10x10
C64: 1N5; C_0805_2012Metric
C67: 330Pf; C_0805_2012Metric
C68: 150pF; C_0805_2012Metric
CONN1: PHASE A; PinHeader_2x04_P2.54mm_Vertical
CONN2: PHASE B; PinHeader_2x04_P2.54mm_Vertical
CONN3: PHASE C; PinHeader_2x04_P2.54mm_Vertical
CONN4: GATE POWER; PinHeader_2x04_P2.54mm_Vertical
CONN5: HV SENSING; PinHeader_2x04_P2.54mm_Vertical
CONN6: FH12-50S-0.5SVA_54_; FH1250S05SVA54; Manufacturer_Part_Number FH12-50S-0.5SVA(54); Mouser Part Number 798-FH1250S0.5SVA54
D1, D2, D3, D4, D5, D6, D7, D8, D9, D15: SMAJ5.0A; DIOM5127X229N; Manufacturer_Part_Number SMAJ5.0A; Mouser Part Number 78-SMAJ5.0A
D10, D12: SMAJ18CA; DIONM5127X229N; Manufacturer_Part_Number SMAJ18CA; Mouser Part Number 652-SMAJ18CA
D11, D14: SS54B; DIOM5336X244N; Manufacturer_Part_Number SS54B
D16: SMAJ7.0A; DIOM5026X229N; Manufacturer_Part_Number SMAJ7.0A; Mouser Part Number 576-SMAJ7.0A
D17: ESDCAN01-2BLY; SOT95P255X150-3N; Manufacturer_Part_Number ESDCAN01-2BLY; Mouser Part Number 511-ESDCAN01-2BLY
F1: JFC2410-0500TS; FUSC6126X280N; Manufacturer_Part_Number JFC2410-0500TS
F2: 1206L050/24WR; Fuse_1206_3216Metric
H1, H2, H3, H4, H5, H6, H7, H8: MountingHole; MountingHole_8mm_ipace
IC1: LM2901; SOIC-14_3.9x8.7mm_P1.27mm
IC2: NCV8452STT3G; SOT230P700X180-4N; Manufacturer_Part_Number NCV8452STT3G; Mouser Part Number 863-NCV8452STT3G
IC3: TDA2822D; SOIC127P600X175-8N; Manufacturer_Part_Number TDA2822D; Mouser Part Number 511-TDA2822D
IC4: CD74HC30M96; SOIC127P600X175-14N; Manufacturer_Part_Number CD74HC30M96; Mouser Part Number 595-CD74HC30M96
IC5: SN65HVD230; SOIC-8_3.9x4.9mm_P1.27mm
IC6: 74LVC3G17DC,125; SOP50P310X100-8N; Manufacturer_Part_Number 74LVC3G17DC,125; Mouser Part Number 771-LVC3G17DC125
IC7: STM32F103VCTx; LQFP-100_14x14mm_P0.5mm
IC8: XL1509-5.0E1; SOIC127P600X175-8N; Manufacturer_Part_Number XL1509-5.0E1
IC9: SN74LVC3G04DCUR; SOP50P310X90-8N; Manufacturer_Part_Number SN74LVC3G04DCUR; Mouser Part Number 595-SN74LVC3G04DCUR
IC10: AMS1117-3.3; SOT-223-3_TabPin2
IC11: MCP6291T-E_OT; SOT95P280X145-5N; Manufacturer_Part_Number MCP6291T-E/OT; Mouser Part Number 579-MCP6291T-E/OT
IC12: SN74LVC3G17DCTR; MSOP-8_3x3mm_P0.65mm; Manufacturer_Part_Number 74LVC3G17DC,125; Mouser Part Number 771-LVC3G17DC125
IC13: SN74LVC1G125DCK; Texas_R-PDSO-G5_DCK-5
J1: 12V TEST; PinHeader_1x02_P2.54mm_Vertical
J2: WiFi serial interface; PinHeader_1x05_P2.54mm_Vertical
J3, J4: SWPROG; PinHeader_1x03_P2.54mm_Vertical
JP1: Termination; SolderJumper-2_P1.3mm_Open_RoundedPad1.0x1.5mm
L1: 10uH 0805; L_0805_2012Metric
L2: 68uH; L_12x12mm_H8mm
L3: 3uH; L_10.4x10.4_H4.8
LED1: 3V3 LED; LED_0805_2012Metric
LED2: ACT LED; LED_0805_2012Metric
Q1, Q2: MMBT3904; SOT-23
R1, R2, R17, R21, R27, R33, R42, R56, R63, R66, R73: 10K; R_0805_2012Metric
R3, R64: 3K9; R_0805_2012Metric
R4: 3K9; R_0805_2012Metric; not fitted
R5, R6, R7, R29, R30, R54: 4K7; R_0805_2012Metric
R8, R12, R23, R24, R25: 1K2; R_0805_2012Metric
R9, R10, R11, R31, R32, R55: 1K5; R_0805_2012Metric
R13, R18: 1K8; R_0805_2012Metric
R14, R22, R26: 2K2; R_0805_2012Metric
R15, R16, R19, R20: 220R; R_0805_2012Metric
R28, R45, R46, R47, R48, R51, R58, R59, R61, R62: 1K; R_0805_2012Metric
R34, R35, R36, R37, R38, R50: 560R; R_0805_2012Metric
R39, R40: 6K2; R_0805_2012Metric
R41: 10R; R_0805_2012Metric
R43, R44: 2K6; R_0805_2012Metric
R49: 0R; R_0805_2012Metric
R52: 2K; R_0805_2012Metric
R53: 120R; R_0805_2012Metric
R57: 27K; R_0805_2012Metric
R60, R69: 680R; R_0805_2012Metric
R65: 47K; R_0805_2012Metric
R67: 1k; R_0805_2012Metric
R68: 6K8; R_0805_2012Metric
R70: 5K1; R_0805_2012Metric
R71, R72: 100R; R_0805_2012Metric
TP1, TP2, TP3, TP4, TP5, TP6, TP7, TP8, TP9, TP10, TP11, TP12, TP13, TP14, TP15, TP16, TP17, TP18, TP19, TP20, TP21, TP22, TP23, TP24, TP25, TP26, TP27: TestPoint; TestPoint_Loop_D2.50mm_Drill1.0mm
Y1: 8MHz; Crystal_SMD_5032-2Pin_5.0x3.2mm

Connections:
+3V3: C38.1, C39.1, C40.1, C42.1, C43.1, C46.1, C47.1, C50.1, C54.1, C55.1, C60.1, C63.1, C66.1, CONN5.2, CONN5.4, D15.1, IC5.3 (VCC), IC6.8 (VCC), IC7.6 (VBAT), IC7.11 (VDD), IC7.28 (VDD), IC7.50 (VDD), IC7.75 (VDD), IC7.100 (VDD), IC9.8 (VCC), IC10.2 (VO), IC12.8 (VCC), IC13.5 (VCC), L1.2, R15.1, R19.1, R60.1, R61.1, R69.1, R72.2
+3V3A: C49.2, C53.1, IC7.21 (VREF+), IC7.22 (VDDA), L1.1
+5V: C11.1, C34.1, C58.1, C61.1, C62.1, C65.1, C69.1, CONN2.6, D16.1, F2.2, IC1.3 (V+), IC4.12 (H), IC4.14 (VCC), IC8.3 (FEEDBACK), IC10.3 (VI), IC11.5 (VDD), J2.1, L3.2, R17.1, R22.2, R23.1, R27.1, R65.2
+12P: CONN6.28, CONN6.29, CONN6.30, CONN6.31, CONN6.32, CONN6.33, CONN6.34, CONN6.35, CONN6.36, CONN6.37, CONN6.38, CONN6.39, CONN6.40, CONN6.41, CONN6.42, CONN6.43, CONN6.44, CONN6.45, CONN6.46, CONN6.47, CONN6.48, CONN6.49, CONN6.50, D11.2, J1.2
+12V: C51.1, C52.1, CONN4.7, D12.1, F1.2, IC2.4 (VD), IC8.1 (VIN), R57.1
/8Mhz Clock: IC7.67 (PA8), IC12.1 (1A), TP15.1
/BKIN: IC7.51 (PB12), R51.1, R52.1, TP6.1
/BMS_IN: IC7.65 (PC8), R62.1
/BRAKE: CONN6.14, D6.1, R29.2
/BRAKE_IN: C19.1, IC7.3 (PE4), R29.1, R31.1
/CANH: CONN6.1, D17.1, IC5.7 (CANH), J4.2, R53.2
/CANL: CONN6.2, D17.2, IC5.6 (CANL), J4.1, JP1.2 (B)
/CANRX0: IC5.4 (R), IC7.70 (PA11)
/CANTX0: IC5.1 (D), IC7.71 (PA12)
/CRUISE: CONN6.22, D7.1, R30.2
/CRUISE_IN: C20.1, IC7.91 (PB5), R30.1, R32.1
/DESAT_IN: IC7.64 (PC7), IC7.66 (PC9), R61.2
/ENC_A: C30.1, IC7.31 (PA6), R42.1
/ENC_B: C21.1, IC7.32 (PA7), R33.1
/EXCA: C33.2, CONN6.17, TP5.1
/EXCB: CONN6.18, R49.1
/EXC_OUT: IC7.83 (PD2), R4.2
/FAULT A HI: CONN1.3, R37.2
/FAULT A LO: CONN1.8, R34.2
/FAULT B HI: CONN2.3, R38.2
/FAULT B LO: CONN2.8, R35.2
/FAULT C HI: CONN3.3, R50.2
/FAULT C LO: CONN3.8, R36.2
/FORWARD: CONN6.7, D3.1, R5.2
/FWD_IN: C4.1, IC7.29 (PA4), R5.1, R9.1
/GATE PSU EN: CONN4.4, IC13.4
/GATE PSU STAT: CONN4.6, R71.1
/GATE PSU STAT IN: IC7.1 (PE2), R71.2
/HFEXC: IC7.63 (PC6), R3.2
/HS_TEMP: CONN1.2, R8.2
/IL1_IN: C31.2, IC1.5 (+), IC1.8 (-), IC7.30 (PA5), R39.2, R43.2, TP4.1
/IL2_IN: C32.2, IC1.7 (+), IC1.10 (-), IC7.35 (PB0), R40.2, R44.2, TP3.1
/I_A: CONN1.5, R39.1
/I_B: CONN2.5, R40.1
/I_C: CONN3.5
/LINK DISCH: IC7.78 (PC10), IC12.6 (3A)
/LINK DISCH_OUT: CONN5.3, IC12.2 (3Y)
/MAIN_PSU_EN: IC7.77 (PA15), IC13.2, R28.2, R58.2
/MOT_TMP1: CONN6.9, D4.1, R12.2
/MOT_TMP2: CONN6.10, D5.1, R25.2
/OCUR_NEG: IC7.93 (PB7), R2.2
/OCUR_POS: IC7.95 (PB8), R1.2
/PWM A HI: CONN1.4, IC9.7 (1Y), TP11.1
/PWM A LO: CONN1.7, IC6.7 (1Y), TP9.1
/PWM B HI: CONN2.4, IC9.5 (2Y), TP12.1
/PWM B LO: CONN2.7, IC6.5 (2Y), TP8.1
/PWM C HI: CONN3.4, IC9.2 (3Y), TP10.1
/PWM C LO: CONN3.7, IC6.2 (3Y), TP7.1
/PWM_1N: IC6.1 (1A), IC7.52 (PB13)
/PWM_1P: IC7.40 (PE9), IC9.1 (1A)
/PWM_2N: IC6.3 (2A), IC7.53 (PB14)
/PWM_2P: IC7.68 (PA9), IC9.3 (2A)
/PWM_3N: IC6.6 (3A), IC7.54 (PB15)
/PWM_3P: IC7.69 (PA10), IC9.6 (3A)
/RES_COSA: C14.1, CONN6.21, R19.2, R20.1
/RES_COSB: CONN6.20, R42.2
/RES_SINA: C10.1, CONN6.23, R15.2, R16.1
/RES_SINB: CONN6.24, R33.2
/REVERSE: CONN6.8, D1.1, R6.2
/REV_IN: C5.1, IC7.26 (PA3), R6.1, R10.1
/START: CONN6.3, D2.1, R7.2
/START_IN: C6.1, IC7.92 (PB6), R7.1, R11.1
/SWCLK: IC7.76 (PA14), J3.3
/SWDAT: IC7.72 (PA13), J3.1
/S/D HV CLK: CONN5.7, IC12.7 (1Y), TP17.1
/S/D HV DATA: CONN5.8, IC12.3 (2A), TP16.1
/T15_IN: CONN6.15, D10.1, R54.1
/T15_OUT: C44.1, IC7.25 (PA2), R54.2, R55.2, R59.2
/THROTTLE 1: CONN6.12, D9.1, R45.2
/THROTTLE 1 IN: C35.1, IC7.16 (PC1), R45.1, R47.1
/THROTTLE 2: CONN6.11, D8.1, R46.2
/THROTTLE 2 IN: C36.1, IC7.15 (PC0), R46.1, R48.1
/TMPHS_IN: C9.1, IC7.33 (PC4), R8.1, R14.1
/TMPM1_IN: C7.1, IC7.17 (PC2), R12.1, R17.2
/TMPM2_IN: C17.1, IC7.24 (PA1), R25.1, R27.2
/TMPWTR_IN: C18.1, IC7.23 (PA0), R24.1, R26.1
/UDC_IN: C67.2, IC7.18 (PC3), IC11.1 (VOUT), IC11.4 (VIN-), R66.2, TP13.1
/USART_RX: IC7.48 (PB11), J2.3
/USART_TX: IC7.47 (PB10), J2.4
/VOUTN: CONN5.6, TP22.1
/VOUTP: CONN5.5, TP21.1
/WTR_TMP1: CONN6.5, R23.2
/WTR_TMP2: CONN6.6, R24.2
GND: C1.2, C2.2, C3.2, C4.2, C5.2, C6.2, C7.2, C8.2, C9.2, C10.2, C11.2, C12.2, C14.2, C15.2, C16.2, C17.2, C18.2, C19.2, C20.2, C21.2, C22.2, C23.2, C24.2, C25.2, C26.2, C27.2, C28.2, C29.2, C30.2, C31.1, C32.1, C34.2, C35.2, C36.2, C37.2, C38.2, C39.2, C40.2, C41.1, C42.2, C43.2, C44.2, C45.1, C46.2, C47.2, C48.1, C49.1, C50.2, C51.2, C52.2, C53.2, C54.2, C55.2, C56.2, C57.2, C58.2, C59.2, C60.2, C61.2, C62.2, C63.2, C64.2, C65.2, C66.2, C68.2, C69.2, CONN1.1, CONN2.1, CONN3.1, CONN4.1, CONN4.3, CONN5.1, D1.2, D2.2, D3.2, D4.2, D5.2, D6.2, D7.2, D8.2, D9.2, D10.2, D12.2, D14.2, D15.2, D16.2, D17.3, H1.1, H2.1, H3.1, H4.1, H5.1, H6.1, H7.1, H8.1, IC1.12 (V-), IC2.2 (GND), IC3.4 (GROUND), IC3.5 (INPUT-(2)_1), IC3.6 (INPUT-(2)_2), IC4.7 (GND), IC5.2 (GND), IC5.8 (Rs), IC6.4 (GND), IC7.10 (VSS), IC7.19 (VSSA), IC7.20 (VREF-), IC7.27 (VSS), IC7.49 (VSS), IC7.74 (VSS), IC7.99 (VSS), IC8.5 (GND_1), IC8.6 (GND_2), IC8.7 (GND_3), IC8.8 (GND_4), IC9.4 (GND), IC10.1 (GND), IC11.2 (VSS), IC12.4 (GND), IC13.1, IC13.3 (GND), J1.1, J2.5, J3.2, J4.3, LED1.1 (K), Q1.2 (E), Q2.2 (E), R9.2, R10.2, R11.2, R14.2, R16.2, R20.2, R21.2, R26.2, R31.2, R32.2, R43.1, R44.1, R47.2, R48.2, R49.2, R52.2, R55.1, R56.1, R62.2, R63.2, R64.1, R66.1, R73.1
unnamed: C3.1, R3.1, R4.1, R13.2, TP1.1
unnamed: C8.1, R13.1, R18.2
unnamed: C12.1, C13.1, R18.1
unnamed: C28.1, C29.1, R41.2
unnamed: C56.1, C57.1, C59.1, L2.2, L3.1
unnamed: C64.1, R67.2, R68.1
unnamed: C67.1, R68.2, R70.1
unnamed: CONN1.6, R72.1
unnamed: CONN2.2, TP19.1
unnamed: CONN3.2, TP20.1
unnamed: CONN3.6, TP23.1
unnamed: CONN4.2, TP18.1
unnamed: CONN4.8, TP24.1
unnamed: CONN6.16, F2.1
unnamed: D11.1, F1.1
unnamed: C2.1, IC1.4 (-), IC1.6 (-), R2.1
unnamed: C1.1, IC1.9 (+), IC1.11 (+), R1.1
unnamed: IC2.3 (IN), R28.1
unnamed: C16.1, IC2.1 (OUT), IC3.2 (SUPPLY_VOLTAGE)
unnamed: C13.2, IC3.7 (INPUT-(1)_1), R21.1
unnamed: C26.1, IC3.8 (INPUT-(1)_2)
unnamed: C33.1, IC3.1 (OUTPUT(1)), R41.1
unnamed: C22.1, IC4.1 (A), R34.1
unnamed: C23.1, IC4.2 (B), R35.1
unnamed: C24.1, IC4.3 (C), R36.1
unnamed: C25.1, IC4.4 (D), R37.1
unnamed: C27.1, IC4.5 (E), R38.1
unnamed: C15.1, IC1.1, IC1.2, IC1.13, IC1.14, IC4.6 (F), R22.1, TP2.1
unnamed: C37.1, IC4.11 (G), R50.1
unnamed: IC4.8 (~Y), R51.2
unnamed: IC7.94 (BOOT0), R56.2
unnamed: C48.2, IC7.14 (NRST)
unnamed: C41.2, IC7.12 (OSC_IN), Y1.1
unnamed: C45.2, IC7.13 (OSC_OUT), Y1.2
unnamed: IC7.37 (PB2), R63.1
unnamed: IC7.34 (PC5), R64.2, R65.1
unnamed: IC7.80 (PC12), LED2.1 (K)
unnamed: IC7.60 (PD13), TP25.1
unnamed: IC7.61 (PD14), TP26.1
unnamed: IC7.62 (PD15), TP27.1
unnamed: IC8.4 (ON/OFF), Q1.3 (C), Q2.3 (C), R57.2
unnamed: D14.1, IC8.2 (OUTPUT), L2.1
unnamed: C68.1, IC11.3 (VIN+), R70.2, TP14.1
unnamed: IC12.5 (2Y), R67.1
unnamed: JP1.1 (A), R53.1
unnamed: LED1.2 (A), R69.2
unnamed: LED2.2 (A), R60.2
unnamed: Q1.1 (B), R58.1, R73.2
unnamed: Q2.1 (B), R59.1

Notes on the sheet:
0V OFF 3V ON
0V OFF 3V OK
PWM DRIVERS
POWER SUPPLY
CONNECTORS
CURRENT SENSORS
RESOLVER
OVERCURRENT AND FAULT
STM32F103VCT6 MCU
GATE PSU ENABLE BUFFER
HIGH SIDE. NONINVERTING.
LOW SIDE. INVERTING.
HV SENSE SIGMA / DELTA
Board Detection
INPUTS DIGITAL / ANALOG
CANBUS
TEMP SENSORS
28-pin inverter connector 1 - Start 2 - Motortemp 1 3 - Throttle 1 4 - Throttle 2 5 - Cruise 6 - Brake 7 - +12v (kl30) 8 - Motortemp 2 9 10 11 12 13 - +15 Ignition (kl15) 14 - +5v Out 15 - CAN-L 16 - Motortemp 1 17 - Resolver SIN S4 18 - Resolver SIN S2 19 - Resolver EXC R2 20 21 22 - CAN-H 23 - Mo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
_- TO DO -_ * Link discharge Logic level or driver needed? * HS_Temp? Seems like CONN1 pin2 and pin4? * Should R27 be 10ohm? It's 10k in M3 * Should we keep the ESD protections on the board even if there is protection circuits on the OEM connector board? Do Not Mount?

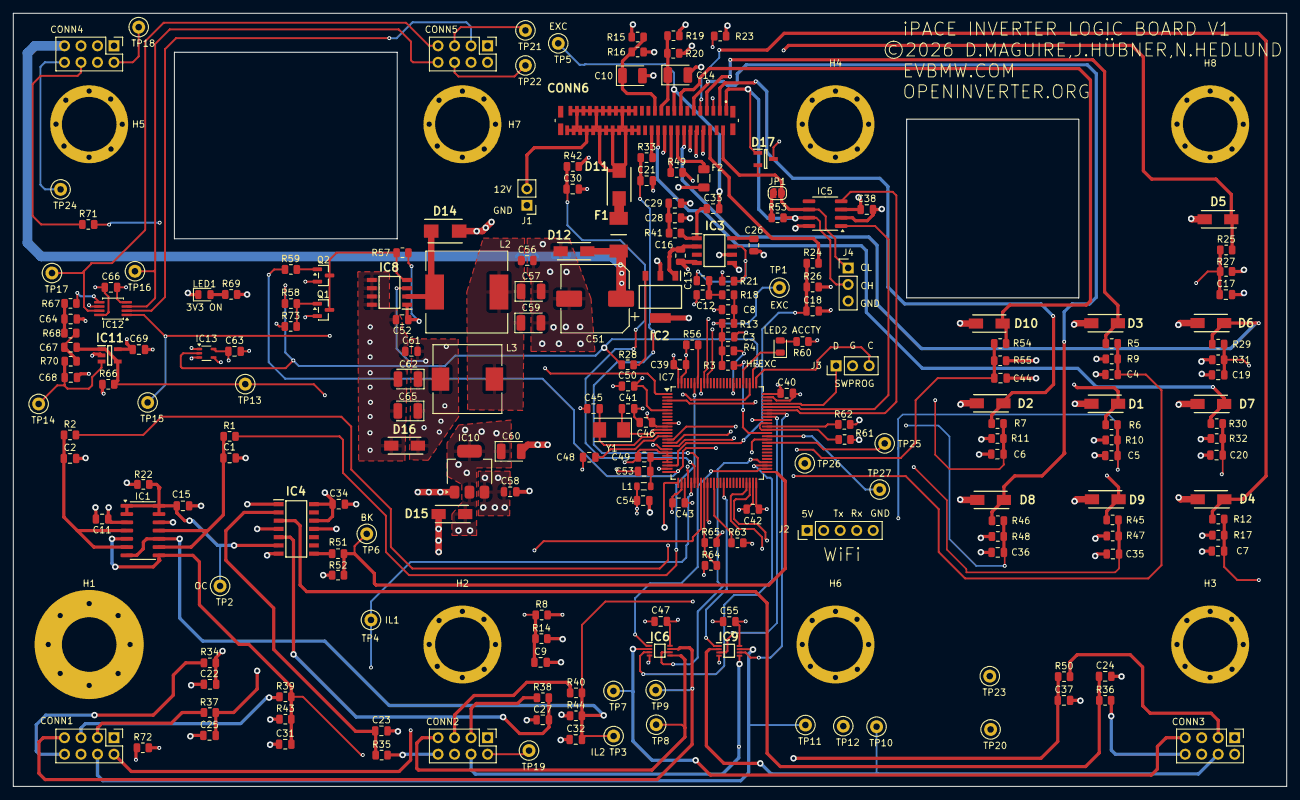
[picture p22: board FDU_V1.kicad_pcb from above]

Board: 6 copper layers, 196.0 x 119.0 mm, 227 parts (0 on the bottom side), 137 nets.

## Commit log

2026-03-27 Add V1 board
    [BOM-FDU_V1.csv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]
2026-03-28 Update design as per order
    [BOM-FDU_V1.csv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]

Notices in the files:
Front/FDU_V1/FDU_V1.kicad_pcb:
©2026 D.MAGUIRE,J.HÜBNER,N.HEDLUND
